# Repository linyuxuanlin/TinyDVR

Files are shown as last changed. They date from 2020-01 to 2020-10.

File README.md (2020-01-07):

# TinyDVR - 小巧身材，满载动力

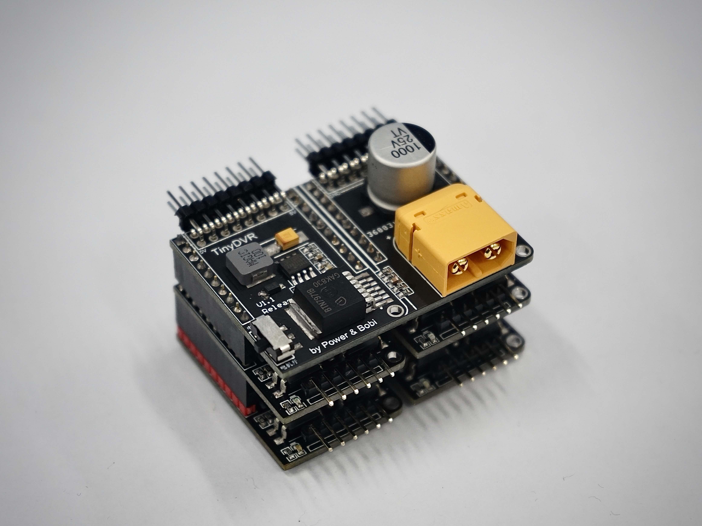
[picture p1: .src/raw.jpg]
raw


TinyDVR 是一款电机驱动套件，包含母板（Master）与子板（Slave），供电部分与驱动部分分离，相比前身 ZenDriver 大幅度缩减了体积，极大提升了可拓展性。你可以根据自己的需要，堆叠不同数量的子板，驱动 n 个电机。

# 基本参数
1. 输入电压：**7.2 ~ 20 V**
2. 输出电流：**0 ~ 68 A**
3. 提供 **5V / 3A** 的电源输出，可供控制器及其他模块使用
4. 保护装置：集成防反接、光耦隔离电路
5. 电机简便接插：对市面上通用的直流减速电机（带编码器），可直接用 6 pin 排线接插（免对线）
5. 可拓展：一块母板可堆叠 n 块子板，实现 n 路电机驱动

# 接口定义

## TinyDVR Master
master

## TinyDVR Slave
slave
背面引脚详解：

* \+ ：提供 5V / 3A 的电源输出
* 1 ：IN1 端口，输入 PWM 信号 1
* 2 ：IN2 端口，输入 PWM 信号 2
* A :  编码器 A 相信号端口
* B :  编码器 B 相信号端口
* \- ：GND

# 使用指南

## 测试方法

1. 接入 **7.2 ~ 20 V** 电池供电
2. 在对应的子板处接上电机
3. 用 **5V** 供电口分别接 **IN1/ IN2** 端口，此时电机将 **正 / 反转**
## 连接单片机

1. 接入 **7.2 ~ 20 V** 电池供电
2. 在对应的子板处接上电机
3. 共地（驱动板 GND 接单片机 GND）
4. IN1，IN2 端口接单片机对应 PWM 端口（代码内设置）
5. 用代码调试：请见 Github 仓库内的 **测试例程**

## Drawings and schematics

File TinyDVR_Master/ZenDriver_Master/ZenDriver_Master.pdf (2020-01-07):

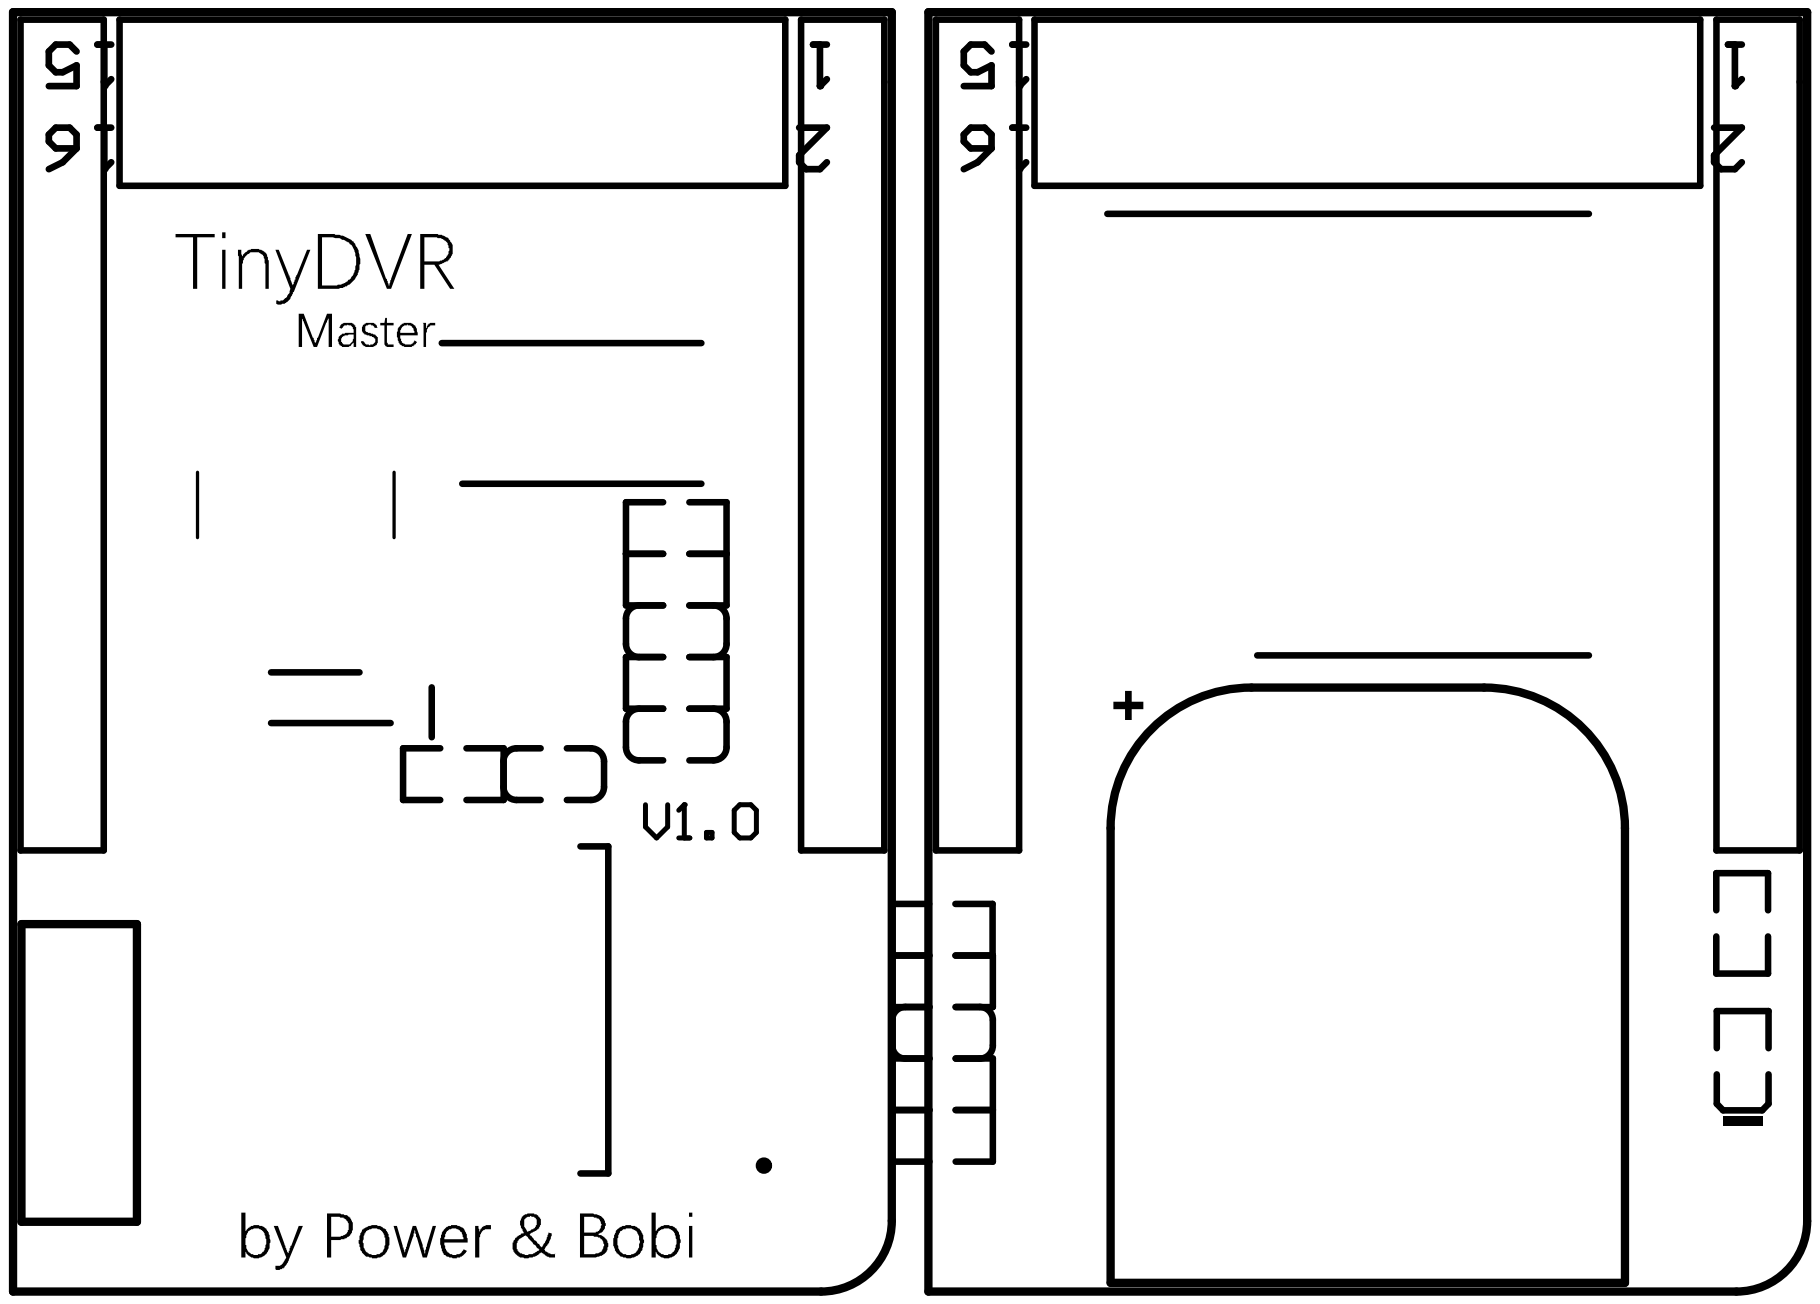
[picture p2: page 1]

Comment | Description | Designator | Footprint | LibRef | Quantity
10uF 4.5V tan | T494D106K035AH | C2 | CAPPM7343X310N | T494D106K035AH | 1
6.8nF (682) 10% 50V | 贴片电容 | C3 | 0603_C | 0603 6.8nF (682) 10% 50V | 1
100nF (104) 10% 50V贴片电容 | | C4 | 0603_C | 0603 100nF (104) 10% 50V | 1
10nF (103) 10% 50V | 贴片电容 | C5 | 0603_C | 0603 10nF (103) 10% 50V | 1
1000uf 25v | Capacitor Polarised | C9 | CAPAE1350X1400N | 8.6506E+11 | 1
100nF (104) 10% 50V贴片电容 | | C10 | 0603_C | 0603 100nF (104) 10% 50V | 1
B130LAW-7-F | Diode | D1 | SOD3716X145N | B130LAW-7-F | 1
红灯 0603 | 发光二极管 | D2 | 0603_LED_S1 | 0603 红灯 | 1
MP1484EN-LF | Integrated Circuit | IC1 | SOIC127P600X170-9NMP1484EN-LF | | 1
1040 10UH 5A | Inductor | L1 | 74404064470 | 74404064100 | 1
Header 10 | Header, 10-Pin | P1 | HDR1X10 | Header 10 | 1
Header 10 | Header, 10-Pin | P2 | HDR1X10 | Header 10 | 1
Header 10 | Header, 10-Pin | P3 | HDR1X10 | Header 10 | 1
Header 10 | Header, 10-Pin | P4 | HDR1X10 | Header 10 | 1
XT60PW-M | XT60 | P7 | XT60PW-M | XT60 | 1
44.2K | 贴片电阻 | R1 | 0603_R | 0603 1.5KΩ (1501) 1% | 1
10KΩ (1002) ±1% | 贴片电阻 | R2 | 0603_R | 0603 10KΩ (1002) 1% | 1
6.8KΩ (6801) ±1% | 贴片电阻 | R3 | 0603_R | 0603 6.8KΩ (6801) 1% | 1
100KΩ (1003) ±1% | 贴片电阻 | R4 | 0603_R | 0603 100KΩ (1003) 1% | 1
4.7k | 贴片电阻 | R7 | 0603_R | 0603 470Ω (4700) 1% | 1
10KΩ (1002) ±1% | 贴片电阻 | R8 | 0603_R | 0603 10KΩ (1002) 1% | 1
10KΩ (1002) ±1% | 贴片电阻 | R9 | 0603_R | 0603 10KΩ (1002) 1% | 1
1KΩ (1001) ±1% | 贴片电阻 | R10 | 0603_R | 0603 1KΩ (1001) 1% | 1
2KΩ (2001) ±1% | 贴片电阻 | R11 | 0603_R | 0603 2KΩ (2001) 1% | 1
SW-SPDT | SPDT Subminiature Toggle Switch, Right Angle Mounting, Vertical Actuation S1 | | sw_9*3.5*5.5mm | SW-SPDT | 1
BTN7971 | | U1 | DPAK127P1615X127-8N BTN7971 | | 1

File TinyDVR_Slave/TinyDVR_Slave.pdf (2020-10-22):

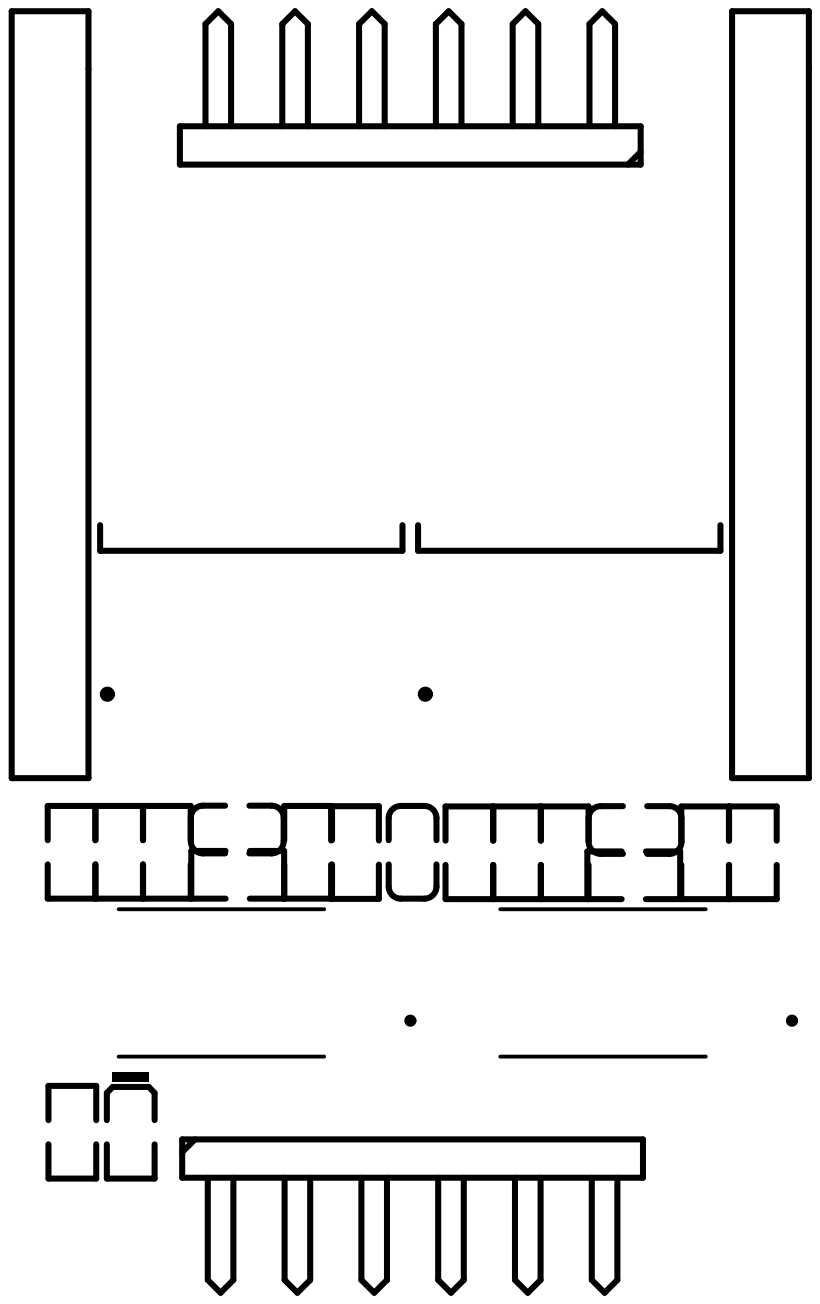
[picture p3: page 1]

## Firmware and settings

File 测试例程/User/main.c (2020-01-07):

/**
  ******************************************************************************
  * @file    main.c 
  * @author  Luu_yy & Power Lin
  * @version 
  * @date    
  * @brief  
  ******************************************************************************
  */  

/* Includes ------------------------------------------------------------------*/

#include "user_code.h"

/**
  * @brief  Main program.
  * @param  None
  * @retval 主函数要尽量的看起来整洁
  */
int main(void)
{
	Init();
}

/******************* (C) COPYRIGHT 2011 STMicroelectronics *****END OF FILE****/

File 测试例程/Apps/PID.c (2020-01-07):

/*
  *******************************************************************************
  * @file    PID.c
  * @author  Luu-yy
  * @version  
  * @date    
  * @brief   PID功能函数
  ******************************************************************************
  */

#include "PID.h"

/*输出限幅*/
void PWM_Limit(int motor)
{
	int Amplitude = 7200;
    if(motor > Amplitude)
		motor = Amplitude;
    if(motor < -Amplitude)
		motor = -Amplitude;
}

/**
* @brief	     增量式PID-参数初始化(试过可用，位置式后来加上去要你们自己试试应该是没问题的）
* @param [in]    增量式PID指针
*				 [in] Kp   比例  主要是提高响应速度
*				 [in] Ki   积分  消除稳态误差
*				 [in] Kd   微分  抑制偏差
*				 具体解析可以看文档和自己百度慢慢摸索，调参很多时候还靠感觉
* @retval        
*/
int Incremental_PID(int Encoder, int Target)
{
	pid.Kp = -150;    
	pid.Ki = -40;
	pid.Kd = 0;

	pid.err = Encoder - Target;
	pid.pwm += pid.Kp*(pid.err - pid.err_last) + pid.Ki*pid.err + pid.Kd*(pid.err - 2 * pid.err_last + pid.err_beforeLast);

	if (pid.pwm>7200)
		pid.pwm = 7200;
	else if (pid.pwm<-7200)
		pid.pwm = -7200;

	pid.err_beforeLast = pid.err_last;
	pid.err_last = pid.err;
	
	return pid.pwm;
}

/**
* @brief	     位置式PID-参数初始化
* @param [in]    位置式PID指针
*				 [in] Kp
*				 [in] Ki
*				 [in] kd
* @retval 
*/
int Position_PID(int Encoder, int Target)
{
	PID.Kp = 0;
	PID.Ki = 0;
	PID.Kd = 0;

	PID.err = Encoder - Target;
	PID.integral_err += PID.err;

	PID.pwm += PID.Kp*PID.err + PID.Ki*PID.integral_err + PID.Kd*(PID.err - PID.err_last);

	if (PID.pwm>7200)
		PID.pwm = 7200;
	else if (PID.pwm<-7200)
		PID.pwm = -7200;

	PID.err_last = PID.err;

	return PID.pwm;
}

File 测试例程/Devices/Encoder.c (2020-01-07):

/*
 ******************************************************************************
 * @file    Encoder.c
 * @author
 * @version
 * @date
 * @brief   编码器AB相（TIM4 CH1  PB6  CH2  PB7)
 ******************************************************************************
 */

#include "Encoder.h"

void Encoder_TIM_GPIO_Config(void)
{
	GPIO_InitTypeDef GPIO_InitStructure;
	
	RCC_APB2PeriphClockCmd(RCC_APB2Periph_GPIOB, ENABLE);
	/*Enable GPIOB Clock*/

	/*Channel pin configuration of timer corresponding to phase AB used in encoder*/
    GPIO_InitStructure.GPIO_Pin =  GPIO_Pin_6 | GPIO_Pin_7;
    GPIO_InitStructure.GPIO_Mode = GPIO_Mode_IN_FLOATING;
    GPIO_Init(GPIOB, &GPIO_InitStructure);
}

void Encoder_TIM_Mode_Config(uint32_t psc1,uint32_t arr1)
{ 	
	TIM_TimeBaseInitTypeDef TIM_TimeBaseInitStruct;
	TIM_ICInitTypeDef TIM_ICInitStruct;
	
    Encoder_TIM_GPIO_Config();
	
	RCC_APB1PeriphClockCmd(RCC_APB1Periph_TIM4, ENABLE);
	
	//配置时基
	TIM_TimeBaseInitStruct.TIM_CounterMode = TIM_CounterMode_Up;
	//TIM向上计数模式
	TIM_TimeBaseInitStruct.TIM_Period = arr1;
	//配置自动重装载寄存器的值
	TIM_TimeBaseInitStruct.TIM_Prescaler = psc1;
	//配置定时器时钟分频
	TIM_TimeBaseInitStruct.TIM_ClockDivision = TIM_CKD_DIV1;
	//时钟分频
	TIM_TimeBaseInitStruct.TIM_RepetitionCounter=0;
	//重复计数器无效0
	TIM_TimeBaseInit(TIM4, &TIM_TimeBaseInitStruct);
	
	//配置输入
	TIM_ICInitStruct.TIM_Channel = TIM_Channel_1;
	TIM_ICInitStruct.TIM_ICPrescaler = TIM_ICPSC_DIV1;
	//输入器不分频
	TIM_ICInitStruct.TIM_ICPolarity = TIM_ICPolarity_Rising;
	//上升沿捕获
	TIM_ICInitStruct.TIM_ICSelection = TIM_ICSelection_DirectTI;
	//映射到IC1
	TIM_ICInitStruct.TIM_ICFilter = 0;
	//不滤波
	TIM_ICInit(TIM4, &TIM_ICInitStruct);
	
	TIM_ICInitStruct.TIM_Channel = TIM_Channel_2;
	TIM_ICInitStruct.TIM_ICPrescaler = TIM_ICPSC_DIV1;
	TIM_ICInitStruct.TIM_ICPolarity = TIM_ICPolarity_Rising;
	TIM_ICInitStruct.TIM_ICSelection = TIM_ICSelection_DirectTI;
	TIM_ICInitStruct.TIM_ICFilter = 0;
	TIM_ICInit(TIM4, &TIM_ICInitStruct);
	
	TIM_EncoderInterfaceConfig(TIM4, TIM_EncoderMode_TI12, TIM_ICPolarity_Rising, TIM_ICPolarity_Rising);
	//使能编码器模式3 0x0003
	
    TIM_ClearFlag(TIM4, TIM_FLAG_Update);	
//    TIM_ITConfig(TIM4, TIM_IT_Update, ENABLE);
	
	TIM_SetCounter(TIM4,0);
	
	TIM_Cmd(TIM4, ENABLE);
}


/*编码器读取对应CNT计数寄存器的值*/
int Read_Encoder(u8 TIMX)   
{
   int Encoder_TIM;    
   switch(TIMX)
	 {
		 case 1:  Encoder_TIM= (short)TIM1 -> CNT;  TIM1 -> CNT=0;break;
	     case 2:  Encoder_TIM= (short)TIM2 -> CNT;  TIM2 -> CNT=0;break;
		 case 3:  Encoder_TIM= (short)TIM3 -> CNT;  TIM3 -> CNT=0;break;	
		 case 4:  Encoder_TIM= (short)TIM4 -> CNT;  TIM4 -> CNT=0;break;	
		 case 5:  Encoder_TIM= (short)TIM5 -> CNT;  TIM5 -> CNT=0;break;
		 case 8:  Encoder_TIM= (short)TIM8 -> CNT;  TIM8 -> CNT=0;break;
		 default: Encoder_TIM=0;
	 }
		return Encoder_TIM;    /*CNT清零*/
}
